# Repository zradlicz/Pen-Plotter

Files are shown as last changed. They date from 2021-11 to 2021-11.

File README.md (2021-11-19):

# Pen Plotter
I designed and built a Pen Plotter to plot generative art. This document is mostly for me in case I waant to come back and improve my design, so I won't go into detail on assembly or how to actually get it working. Feel free to use the STLs to print your own. I will warn you some of the hole sizes are too small for the harware and shafts, and a lot of dremel work was required to get it to fit together. I lost my Inventor liscense before I got to make improvements, so I'm just calling this project finished.

<p float="left">




<p/>

### Arduino
Arduino folder contains grbl which has been modified to control a servo on the xlim pin. This is necessary for the pen to move up and down.
### GCode
The Gcode folder contains two python scripts to write gcode to a file which can then be used to upload to Universal GCode Sender. The Pen plotter then connects to UGS and runs.

## BOM
Part | Quantity | Price | Link
----- | ------- | ------- | ------
**3D PRINT**| | |
X_STATIC_END | 1 | N/A | N/A
X_MOVING_END | 1 | N/A | N/A
PLATFORM | 2 | N/A | N/A
PEN_HOLDER | 1 | N/A | N/A
MOTOR_MOUNT | 2 | N/A | N/A
BELT_HOLDER | 2 | N/A | N/A
**Timing Belt**| | |
GT2 Timing Belt 2mm pitch 6mm wide | 1 | $4.00 | https://www.amazon.com/dp/B0776KXY8G?psc=1&ref=ppx_yo2_dt_b_product_details
GT2 Timing Pulley 5mm 20 Teeth with Set Screw | 2 | $1.50 | https://www.amazon.com/dp/B0776KXY8G?psc=1&ref=ppx_yo2_dt_b_product_details
GT2 Timing Pulley Toothless 3mm Bore 6mm width | 4 | $1.60 | https://www.amazon.com/dp/B01H3FNZ4M?ref=ppx_yo2_dt_b_product_details&th=1
GT2 Timing Pulley Idler 3mm Bore 20 teeth| 1 | $1.40 | https://www.amazon.com/dp/B01H3DSGAC?ref=ppx_yo2_dt_b_product_details&th=1
**Axis** | | |
6mm x 300mm Linear Motion Rod Shaft | 4 | $3.44 | https://www.amazon.com/dp/B08HYF2WPX?ref=ppx_yo2_dt_b_product_details&th=1
LM6UU Linear Ball Bearing 6mm Bore 12mm OD 35mm Length | 4 | $3.00 | https://www.amazon.com/dp/B08NYJ72Z2?ref=ppx_yo2_dt_b_product_details&th=1
**Motion Control**| | |
Nema 17 Stepper Motor 45Ncm 1.8 degree | 2 | $9.00 | https://www.amazon.com/dp/B074T9ZZFJ?psc=1&ref=ppx_yo2_dt_b_product_details
9g Micro Servo | 1 | $2.74 | https://www.amazon.com/dp/B07MLR1498?ref=ppx_yo2_dt_b_product_details&th=1
CNC Shield Arduino Kit | 1 | $24.00 | https://www.amazon.com/dp/B06XHKSVTG?ref=ppx_yo2_dt_b_product_details&th=1
**Hardware**| | |
M3x20 Screw | 8 | $.10 | https://www.amazon.com/dp/B01NBOCXHE?ref=ppx_yo2_dt_b_product_details&th=1
M3x12 Screw | 2 | $.10 | https://www.amazon.com/dp/B01NBOCXHE?ref=ppx_yo2_dt_b_product_details&th=1
M3x25 Screw | 2 | $.10 | https://www.amazon.com/dp/B01NBOCXHE?ref=ppx_yo2_dt_b_product_details&th=1
3mm x 20mm Round Shaft | 4 | $1.00 | https://www.amazon.com/dp/B07JNP45G9?
**TOTAL**| |**$89.96**|

### Setup
Here is the list of GRBL Parameters I found to work the best.

$0=10
$1=25
$2=0
$3=0
$4=0
$5=0
$6=0
$10=1
$11=0.010
$12=0.002
$13=0
$20=0
$21=0
$22=0
$23=0
$24=25.000
$25=500.000
$26=250
$27=1.000
$30=1000
$31=0
$32=0
$100=84.000
$101=84.000
$102=250.000
$110=4000.000
$111=4000.000
$112=500.000
$120=200.000
$121=200.000
$122=10.000
$130=200.000
$131=200.000
$132=200.000

## Example Work

<p float="left">
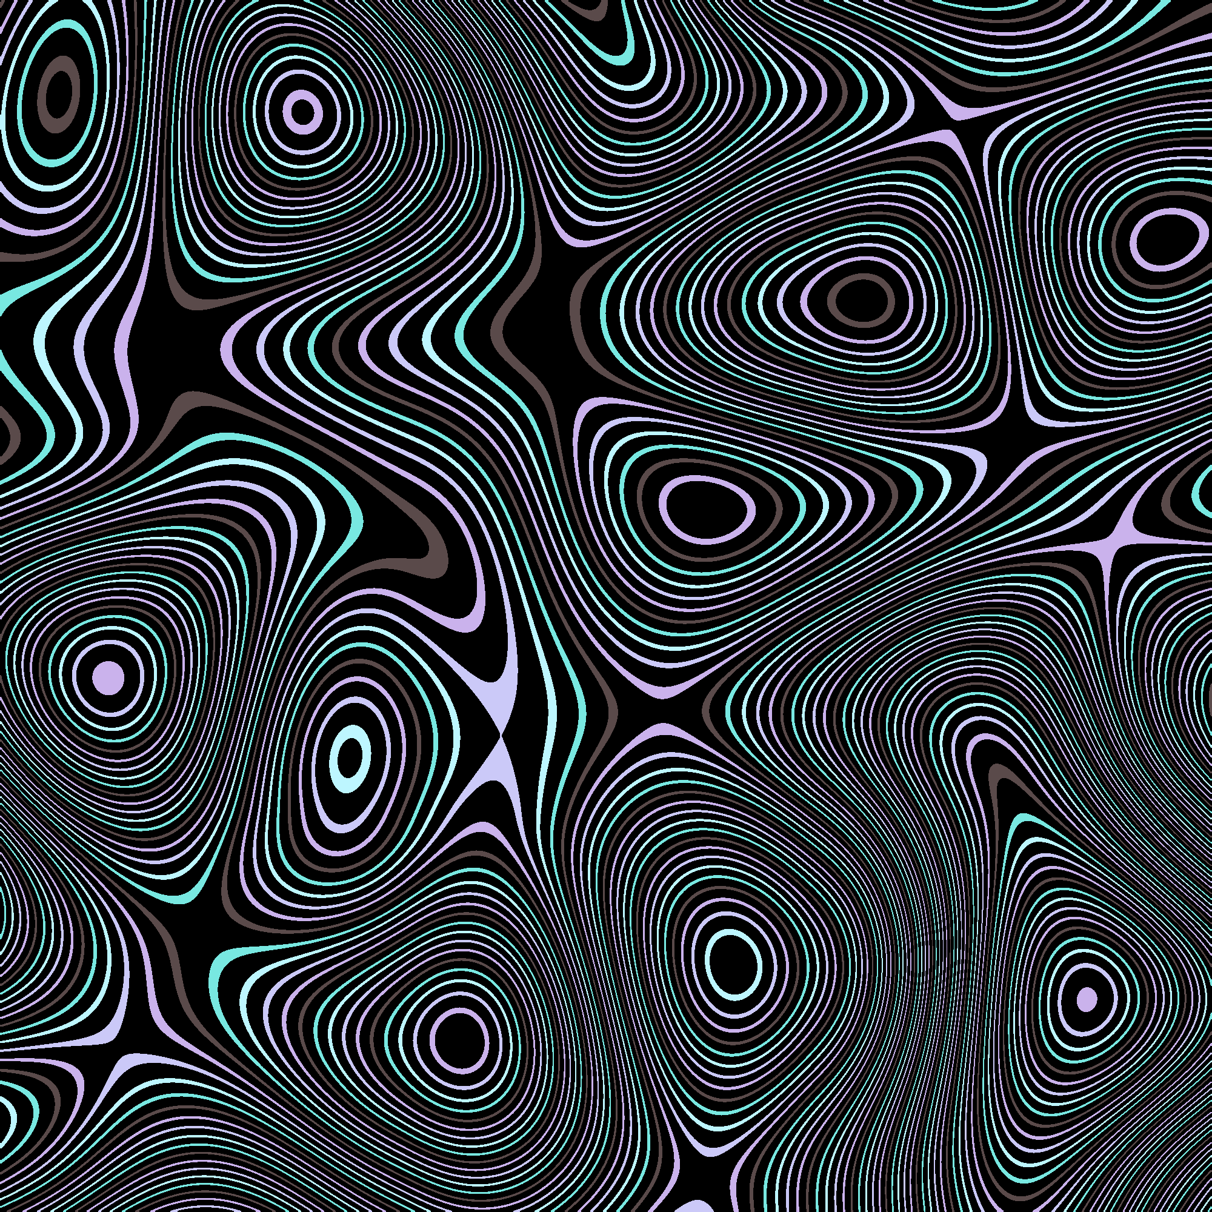
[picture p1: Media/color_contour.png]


<p/>

On the left is the generated image, on the right is the plotter plot. It is not as smooth or accurate as I want, and color changing is done by hand which causes some inaccuracy. The Gcode script to generate GCode also has some bugs which cause the discontinuites at some of the edges. Also my cat moved the machine a little bit at the very end.

## List of Design Improvements
- Pen Holder is too thin and has to much deflection in Y direction  
- Wires get in the way during printing  
- Design electronics box  
- Use set screws to hold shafts in place rather than press fit

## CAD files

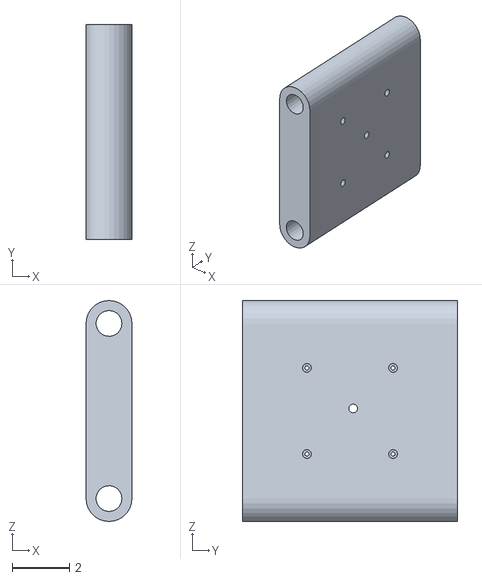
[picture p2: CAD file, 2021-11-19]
STLs/PLATFORM.stl
1.60 x 7.50 x 7.70

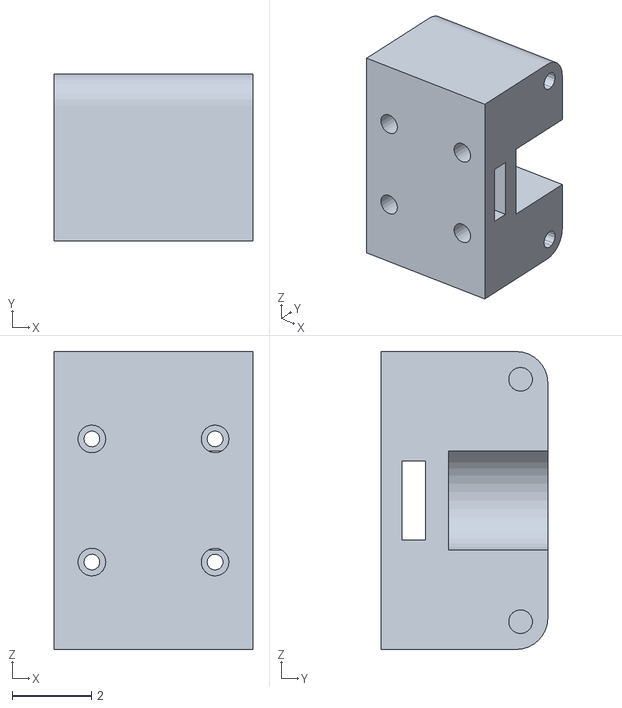
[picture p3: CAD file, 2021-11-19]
STLs/MOTOR_MOUNT.stl
5.00 x 4.20 x 7.50

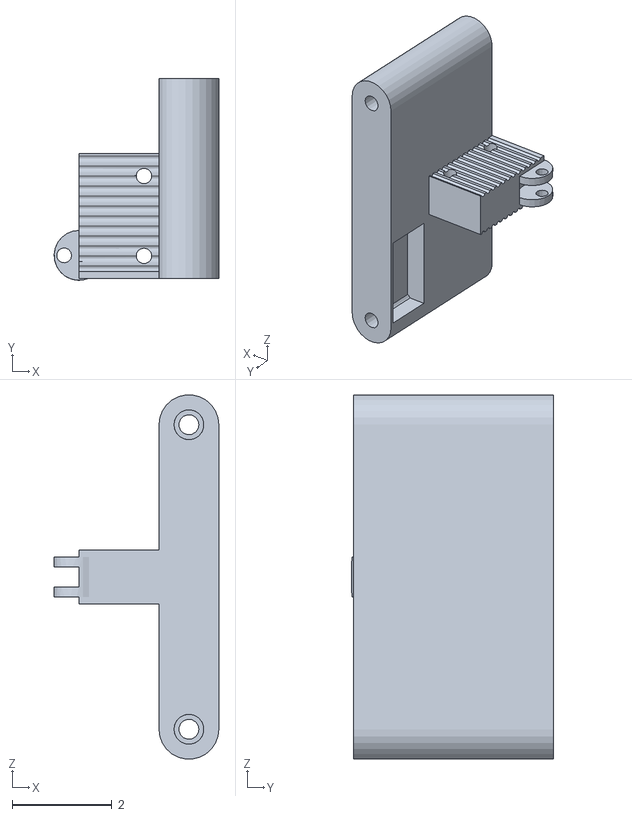
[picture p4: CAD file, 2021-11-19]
STLs/X_STATIC_END.stl
3.30 x 4.04 x 7.29

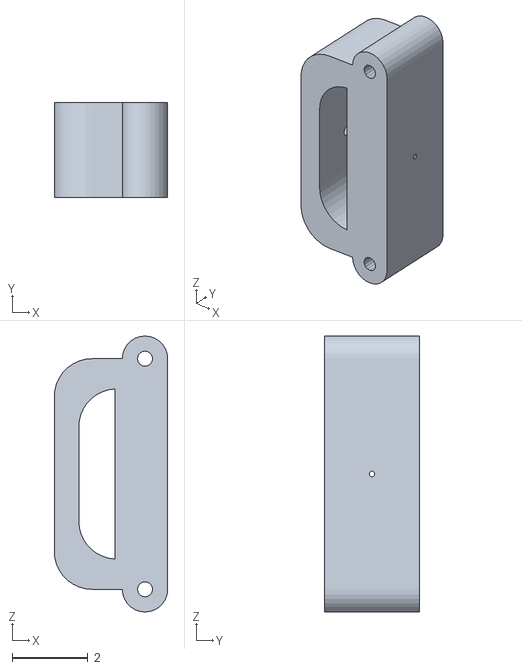
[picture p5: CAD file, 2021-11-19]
STLs/X_MOVING_END.stl
3.00 x 2.50 x 7.30

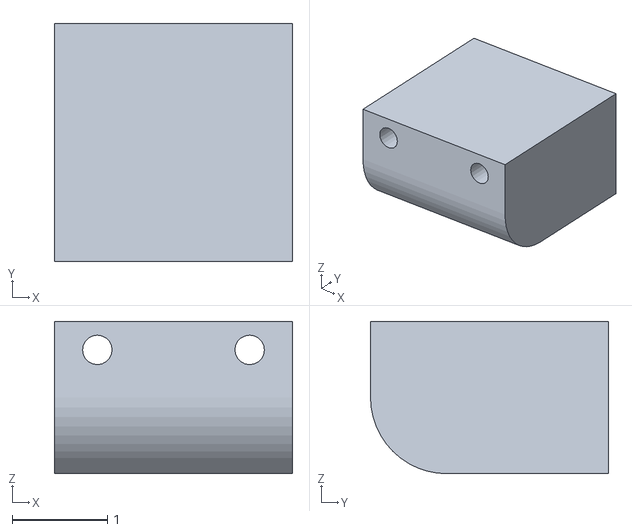
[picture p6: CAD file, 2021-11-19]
STLs/BELT_HOLDER.stl
2.50 x 2.50 x 1.60

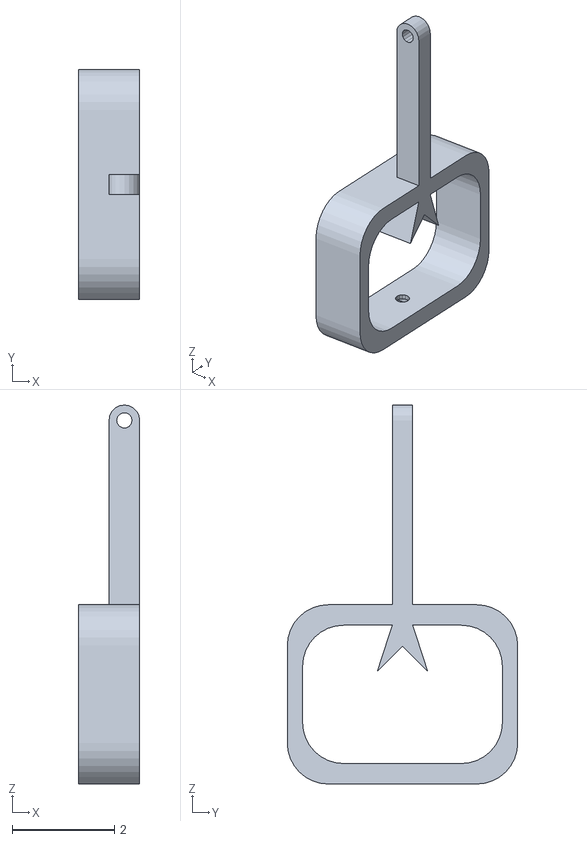
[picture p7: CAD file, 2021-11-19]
STLs/PEN_HOLDER.stl
1.20 x 4.50 x 7.40

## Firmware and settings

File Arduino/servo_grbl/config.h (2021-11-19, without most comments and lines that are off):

#define config_h
#include "grbl.h" // For Arduino IDE compatibility.
#define DEFAULTS_GENERIC
#define CPU_MAP_ATMEGA328P_SERVO // Arduino Uno CPU
#define BAUD_RATE 115200
#define CMD_RESET 0x18 // ctrl-x.
#define CMD_STATUS_REPORT '?'
#define CMD_CYCLE_START '~'
#define CMD_FEED_HOLD '!'
#define CMD_SAFETY_DOOR 0x84
#define CMD_JOG_CANCEL  0x85
#define CMD_DEBUG_REPORT 0x86 // Only when DEBUG enabled, sends debug report in '{}' braces.
#define CMD_FEED_OVR_RESET 0x90         // Restores feed override value to 100%.
#define CMD_FEED_OVR_COARSE_PLUS 0x91
#define CMD_FEED_OVR_COARSE_MINUS 0x92
#define CMD_FEED_OVR_FINE_PLUS  0x93
#define CMD_FEED_OVR_FINE_MINUS  0x94
#define CMD_RAPID_OVR_RESET 0x95        // Restores rapid override value to 100%.
#define CMD_RAPID_OVR_MEDIUM 0x96
#define CMD_RAPID_OVR_LOW 0x97
#define CMD_SPINDLE_OVR_RESET 0x99      // Restores spindle override value to 100%.
#define CMD_SPINDLE_OVR_COARSE_PLUS 0x9A
#define CMD_SPINDLE_OVR_COARSE_MINUS 0x9B
#define CMD_SPINDLE_OVR_FINE_PLUS 0x9C
#define CMD_SPINDLE_OVR_FINE_MINUS 0x9D
#define CMD_SPINDLE_OVR_STOP 0x9E
#define CMD_COOLANT_FLOOD_OVR_TOGGLE 0xA0
#define CMD_COOLANT_MIST_OVR_TOGGLE 0xA1
#define HOMING_INIT_LOCK // Comment to disable
#define HOMING_CYCLE_0 (1<<X_AXIS)  // COREXY COMPATIBLE: First home X
#define HOMING_CYCLE_1 (1<<Y_AXIS)  // COREXY COMPATIBLE: Then home Y
#define N_HOMING_LOCATE_CYCLE 1 // Integer (1-128)
#define N_STARTUP_LINE 2 // Integer (1-2)
#define N_DECIMAL_COORDVALUE_INCH 4 // Coordinate or position value in inches
#define N_DECIMAL_COORDVALUE_MM   3 // Coordinate or position value in mm
#define N_DECIMAL_RATEVALUE_INCH  1 // Rate or velocity value in in/min
#define N_DECIMAL_RATEVALUE_MM    0 // Rate or velocity value in mm/min
#define N_DECIMAL_SETTINGVALUE    3 // Decimals for floating point setting values
#define N_DECIMAL_RPMVALUE        0 // RPM value in rotations per min.
#define MESSAGE_PROBE_COORDINATES // Enabled by default. Comment to disable.
#define SAFETY_DOOR_SPINDLE_DELAY 4.0 // Float (seconds)
#define SAFETY_DOOR_COOLANT_DELAY 1.0 // Float (seconds)
 #define COREXY // Default disabled. Uncomment to enable.
#define CHECK_LIMITS_AT_INIT
#define DEFAULT_FEED_OVERRIDE           100 // 100%. Don't change this value.
#define MAX_FEED_RATE_OVERRIDE          200 // Percent of programmed feed rate (100-255). Usually 120% or 200%
#define MIN_FEED_RATE_OVERRIDE           10 // Percent of programmed feed rate (1-100). Usually 50% or 1%
#define FEED_OVERRIDE_COARSE_INCREMENT   10 // (1-99). Usually 10%.
#define FEED_OVERRIDE_FINE_INCREMENT      1 // (1-99). Usually 1%.
#define DEFAULT_RAPID_OVERRIDE  100 // 100%. Don't change this value.
#define RAPID_OVERRIDE_MEDIUM    50 // Percent of rapid (1-99). Usually 50%.
#define RAPID_OVERRIDE_LOW       25 // Percent of rapid (1-99). Usually 25%.
#define DEFAULT_SPINDLE_SPEED_OVERRIDE    100 // 100%. Don't change this value.
#define MAX_SPINDLE_SPEED_OVERRIDE        200 // Percent of programmed spindle speed (100-255). Usually 200%.
#define MIN_SPINDLE_SPEED_OVERRIDE         10 // Percent of programmed spindle speed (1-100). Usually 10%.
#define SPINDLE_OVERRIDE_COARSE_INCREMENT  10 // (1-99). Usually 10%.
#define SPINDLE_OVERRIDE_FINE_INCREMENT     1 // (1-99). Usually 1%.
#define RESTORE_OVERRIDES_AFTER_PROGRAM_END // Default enabled. Comment to disable.
#define REPORT_FIELD_PIN_STATE // Default enabled. Comment to disable.
#define REPORT_FIELD_WORK_COORD_OFFSET // Default enabled. Comment to disable.
#define REPORT_FIELD_OVERRIDES // Default enabled. Comment to disable.
#define REPORT_FIELD_LINE_NUMBERS // Default enabled. Comment to disable.
#define REPORT_OVR_REFRESH_BUSY_COUNT 20  // (1-255)
#define REPORT_OVR_REFRESH_IDLE_COUNT 10  // (1-255) Must be less than or equal to the busy count
#define REPORT_WCO_REFRESH_BUSY_COUNT 30  // (2-255)
#define REPORT_WCO_REFRESH_IDLE_COUNT 10  // (2-255) Must be less than or equal to the busy count
#define ACCELERATION_TICKS_PER_SECOND 100
#define ADAPTIVE_MULTI_AXIS_STEP_SMOOTHING  // Default enabled. Comment to disable.
#define TOOL_LENGTH_OFFSET_AXIS Z_AXIS // Default z-axis. Valid values are X_AXIS, Y_AXIS, or Z_AXIS.
#define MINIMUM_JUNCTION_SPEED 0.0 // (mm/min)
#define MINIMUM_FEED_RATE 1.0 // (mm/min)
#define N_ARC_CORRECTION 12 // Integer (1-255)
#define ARC_ANGULAR_TRAVEL_EPSILON 5E-7 // Float (radians)
#define DWELL_TIME_STEP 50 // Integer (1-255) (milliseconds)
#define ENABLE_RESTORE_EEPROM_WIPE_ALL         // '$RST=*' Default enabled. Comment to disable.
#define ENABLE_RESTORE_EEPROM_DEFAULT_SETTINGS // '$RST=$' Default enabled. Comment to disable.
#define ENABLE_RESTORE_EEPROM_CLEAR_PARAMETERS // '$RST=#' Default enabled. Comment to disable.
#define ENABLE_BUILD_INFO_WRITE_COMMAND // '$I=' Default enabled. Comment to disable.
#define FORCE_BUFFER_SYNC_DURING_EEPROM_WRITE // Default enabled. Comment to disable.
#define FORCE_BUFFER_SYNC_DURING_WCO_CHANGE // Default enabled. Comment to disable.
#define PARKING_AXIS Z_AXIS // Define which axis that performs the parking motion
#define PARKING_TARGET -5.0 // Parking axis target. In mm, as machine coordinate [-max_travel,0].
#define PARKING_RATE 500.0 // Parking fast rate after pull-out in mm/min.
#define PARKING_PULLOUT_RATE 100.0 // Pull-out/plunge slow feed rate in mm/min.
#define PARKING_PULLOUT_INCREMENT 5.0 // Spindle pull-out and plunge distance in mm. Incremental distance.
#define N_PIECES 4  // Integer (1-4). Number of piecewise lines used in script solution.
#define RPM_MAX  11686.4  // Max RPM of model. $30 > RPM_MAX will be limited to RPM_MAX.
#define RPM_MIN  202.5    // Min RPM of model. $31 < RPM_MIN will be limited to RPM_MIN.
#define RPM_POINT12  6145.4  // Used N_PIECES >=2. Junction point between lines 1 and 2.
#define RPM_POINT23  9627.8  // Used N_PIECES >=3. Junction point between lines 2 and 3.
#define RPM_POINT34  10813.9 // Used N_PIECES = 4. Junction point between lines 3 and 4.
#define RPM_LINE_A1  3.197101e-03  // Used N_PIECES >=1. A and B constants of line 1.
#define RPM_LINE_B1  -3.526076e-1
#define RPM_LINE_A2  1.722950e-2   // Used N_PIECES >=2. A and B constants of line 2.
#define RPM_LINE_B2  8.588176e+01
#define RPM_LINE_A3  5.901518e-02  // Used N_PIECES >=3. A and B constants of line 3.
#define RPM_LINE_B3  4.881851e+02
#define RPM_LINE_A4  1.203413e-01  // Used N_PIECES = 4. A and B constants of line 4.
#define RPM_LINE_B4  1.151360e+03

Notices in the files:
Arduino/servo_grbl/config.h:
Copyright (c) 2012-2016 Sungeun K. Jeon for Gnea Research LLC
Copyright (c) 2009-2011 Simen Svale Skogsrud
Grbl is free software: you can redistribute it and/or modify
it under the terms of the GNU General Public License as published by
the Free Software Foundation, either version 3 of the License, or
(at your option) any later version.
